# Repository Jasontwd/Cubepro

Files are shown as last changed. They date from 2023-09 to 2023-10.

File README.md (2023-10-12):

# Supercharged 3D Systems Cube Pro Trio
## New Twin hotend rebuild into a high temperature production printer

Having access to the high quality 3DXTech filaments meant that I could take an old Cube Pro Trio and turn it into a fast high-temperature production printer.  This means I can now use various types of filaments including water soluble supports. Including High Temp filaments up to 420deg C

This has taken my 3D printing to another level, and means there is less waste and less issues.  When it comes to filaments, you get what you pay for - so when quality matters, the 3DXTech filaments are fantastic. 

------------------------------------------------------------------------------------------------------------------------------------------------------------------------------------------------------------------------

## <b>History on this build</b>

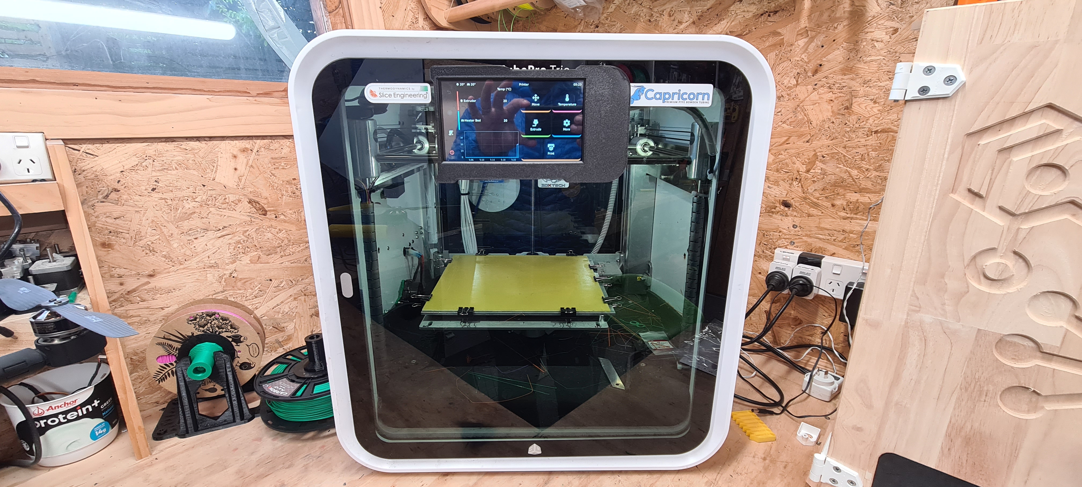
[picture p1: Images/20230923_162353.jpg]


These days there are lots of old 2nd hand printers out there in the market that sometimes need a new lease on life.

3D Systems produced their desktop Cube Pro Duo and trio several years ago and sent them off into mass manufacture.

They are out there for a good deal, if you are patient and can find one.  I found mine on Trade Me.  Also check out eBay and hit up your network.

Built like the proverbial 'brick shit house', these machines were slow but did a great job. The internal drive train, stepper motors, rails and enclosure are generally built very well, they form a solid basis of a good rebuild.

The professional looking enclosure is also well made, from Aluminum composite panel (ACP) with a LCD in built and glass door to top it all off.

Proprietary software and filament cases (with electronic chip) meant you where locked into their software and their filament.  In New Zealand it was hard to source filaments, which is frustrating and limits what you can do with the machine.

I found my printer on Trade Me in mid 2019, after a mate had also bought 2.

-----------------------------------------------------------------------------------------------------------------------------------------------------------------------------------------------------------------------------------
## <b>Specifications of the new machine, after its rebuild</b>

Cube Pro Duo Mosquito Liquid, water cooled high volume printer

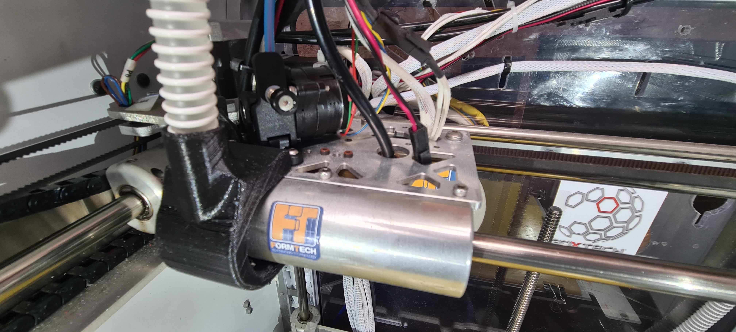
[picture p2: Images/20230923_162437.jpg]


Retrofitted electrics, Open Source main board with Raspberry Pi4 to complement the existing drive train on board the Cube Pro

- Klipper firmware and front panel klipper screen.
- Flyboard 64 main board.
- Raspberry PI 4 klipper headless on board, with wifi.
- Twin Liquid Mosquitos water cooled from Slice Engineering.
- 450deg rated heat blocks and heaters for PEKK etc.
- Obitor V2 twin extruders
- Heated 310mm square aluminum build plate 750w  230v AC bed ( 30sec heat up time to 120deg C)
- On board Rpi Camera wide angle for AI print detection
- High speed CPAP 12v part cooling fan
- 2 filament bays internal for pre drying capacity, great for ABS and Nylon 910 
- Enclosure ventilation suction fan 40mm rear mounted to external vent for ABS and PEKK printing
- Flexible filaments and water soluble supports printed easy as
- 24v 650w Power supply on board for all equipment, the existing one thats on the right.
- 5v PSU power supply on board for Rpi 4 (dedicated supply)
- Cube pro enclosure, insulated and isolated from electrics for heating enclosure internal for better fusion on prints.
- PEKK, PEEK and Carbon reinforced print ready
-------------------------------------------------------------------------------------------------------------------
## Water cooling
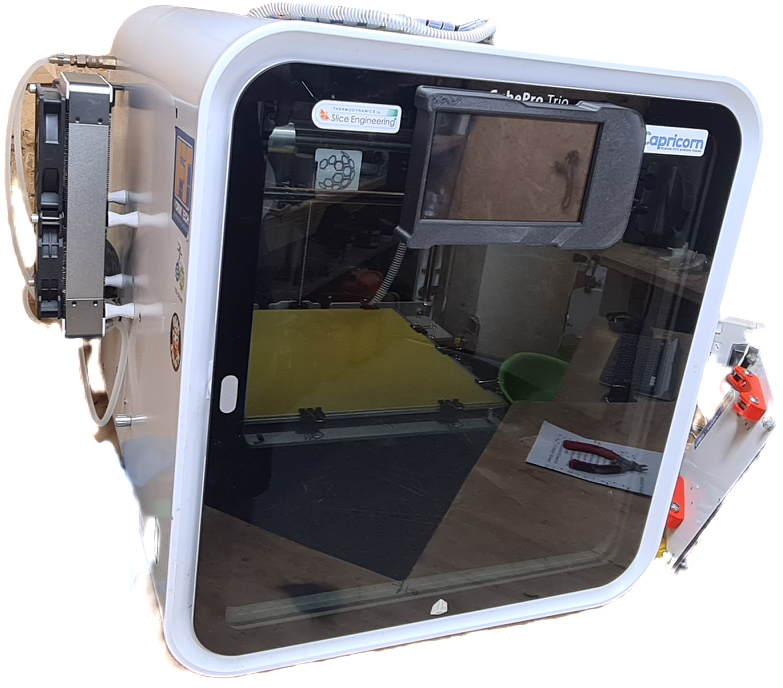
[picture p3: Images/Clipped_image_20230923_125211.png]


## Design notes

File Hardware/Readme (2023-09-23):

## CPAP Fans

Image of fan here:
https://www.aliexpress.com/item/33041228096.html?spm=a2g0o.order_list.order_list_main.21.68c11802tUSnGA

12mm CPAP hose locla to NZ
https://www.cpap.co.nz/collections/tubing/products/200-series-non-heated-tubing

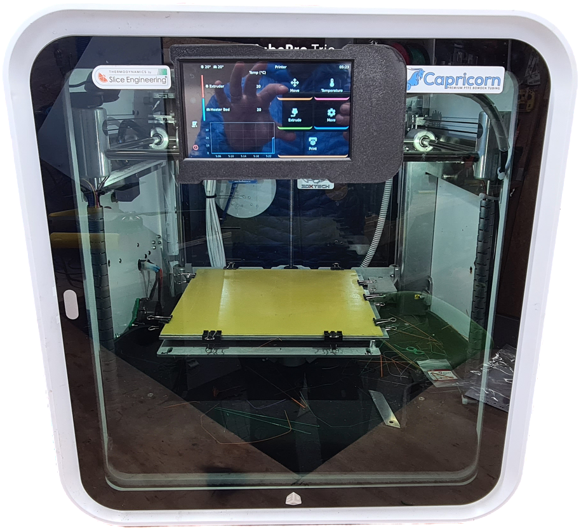
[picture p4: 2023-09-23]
Images/Clipped_image_20230923_163300.png

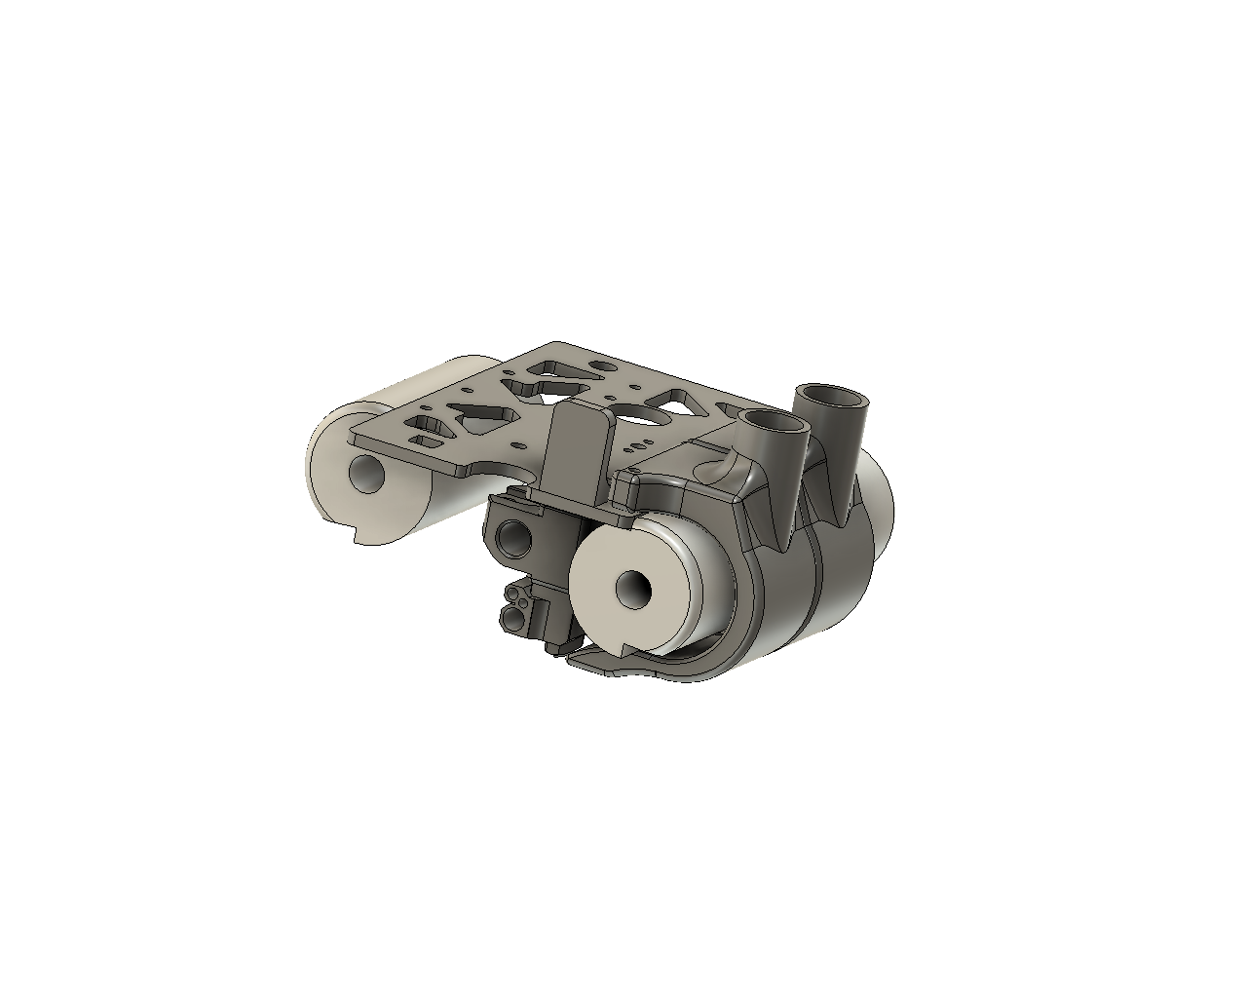
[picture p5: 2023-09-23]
CAD files/Isometric X gantry.png

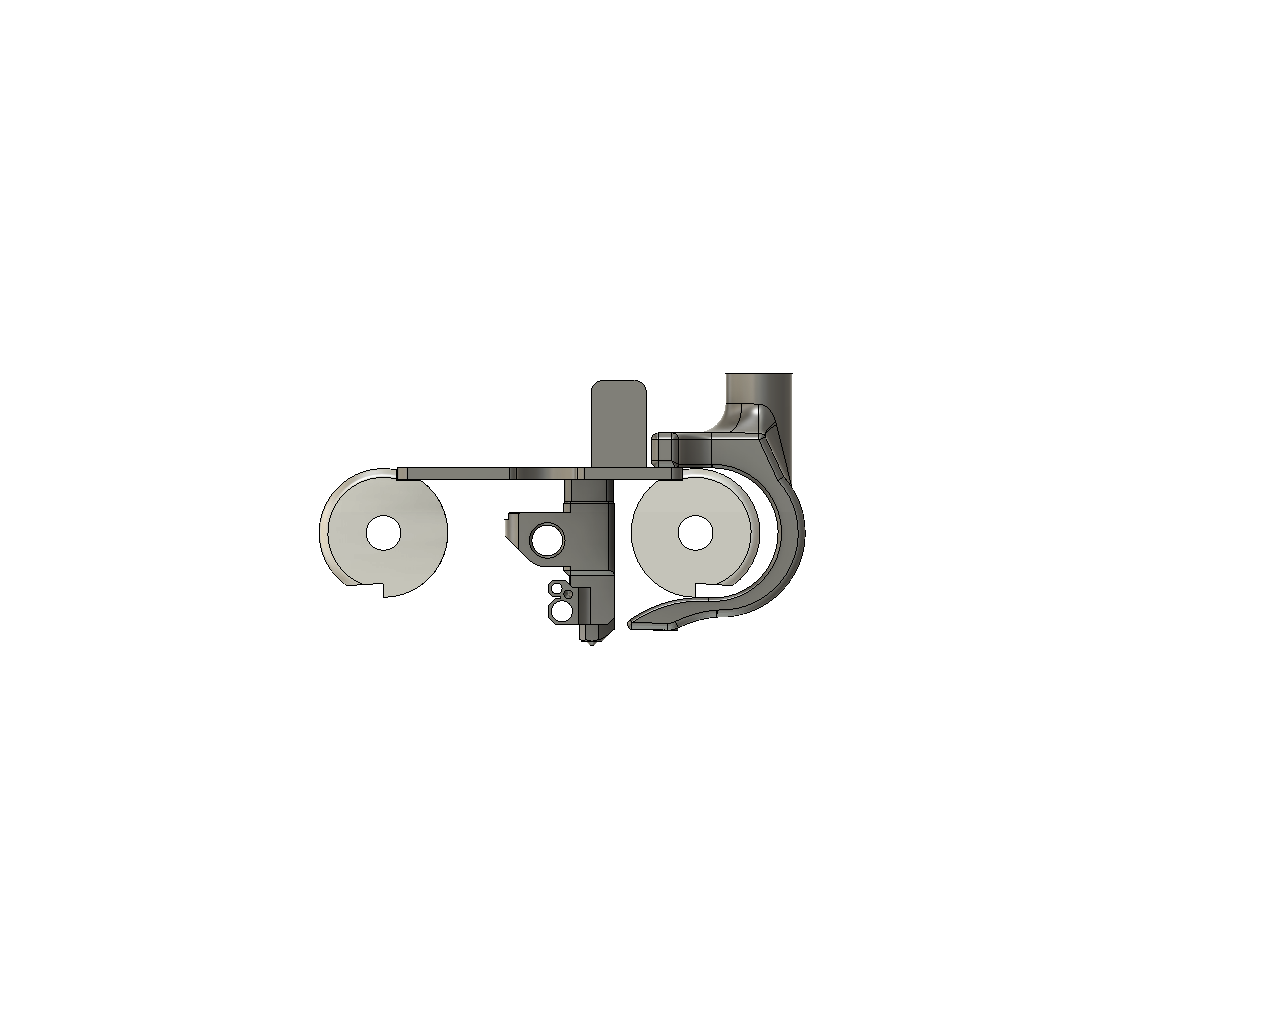
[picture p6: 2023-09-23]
CAD files/Side shot X gantry.png

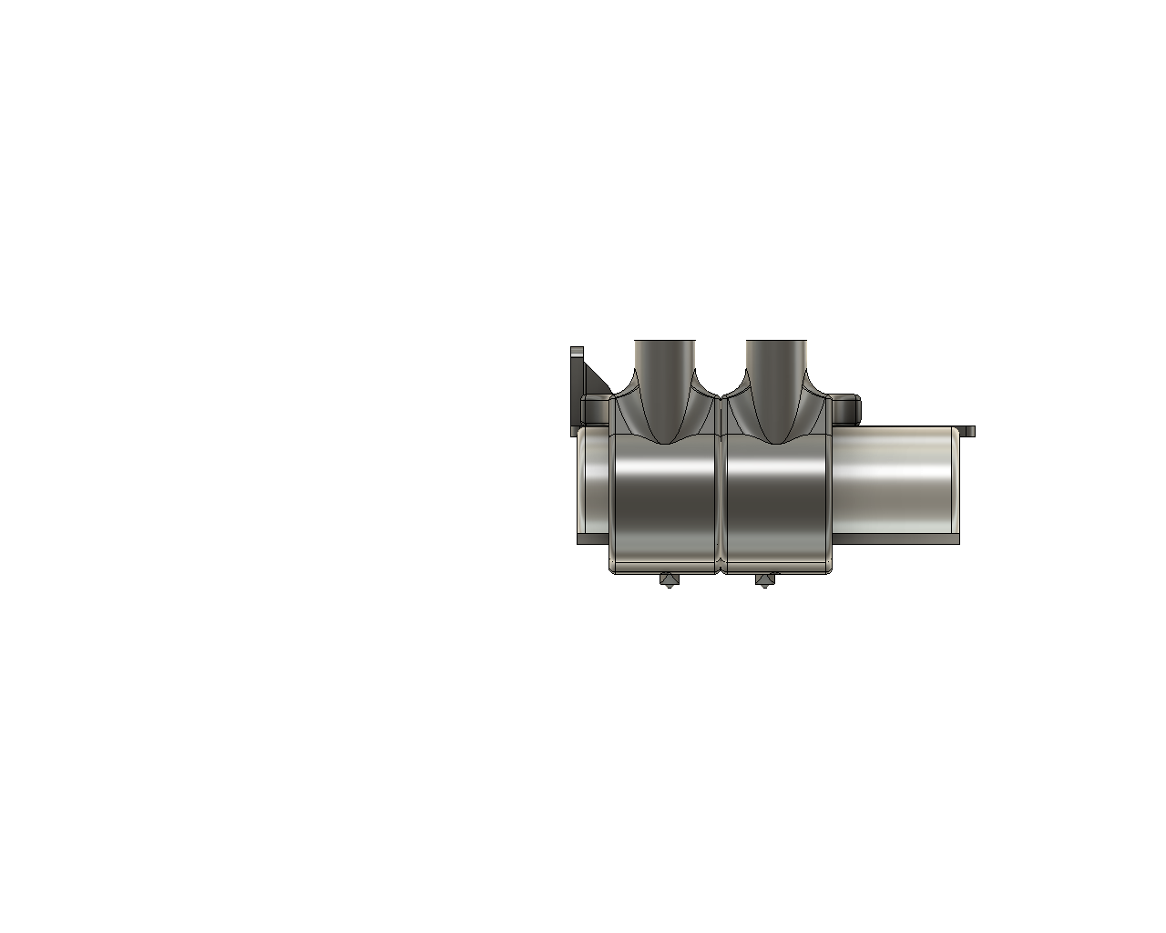
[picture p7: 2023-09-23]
CAD files/Front shot X gantry.png

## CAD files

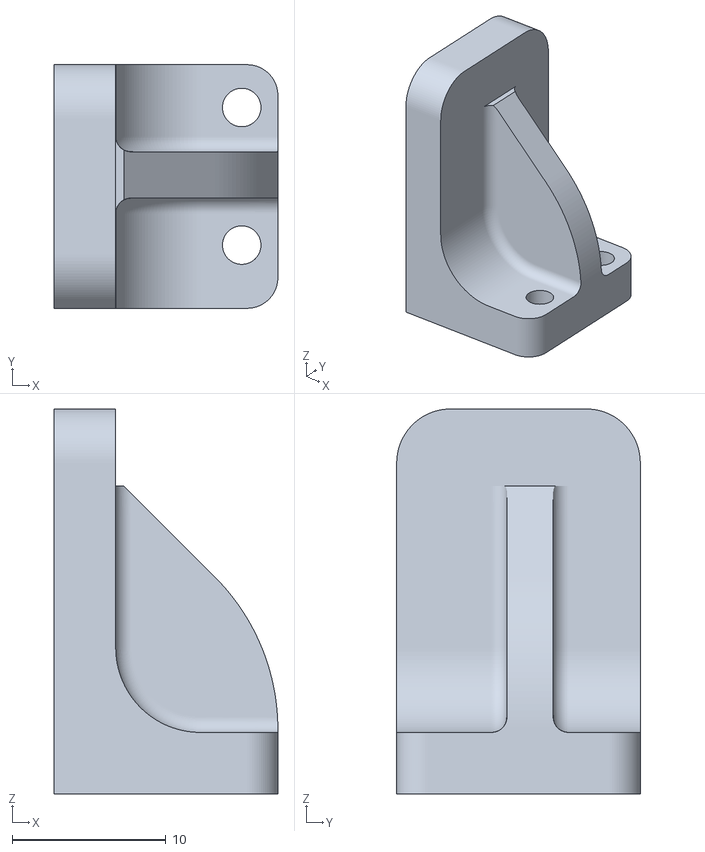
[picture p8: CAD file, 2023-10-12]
3D Printing files/X carridge endstop.stl
14.5 x 15.8 x 25.0

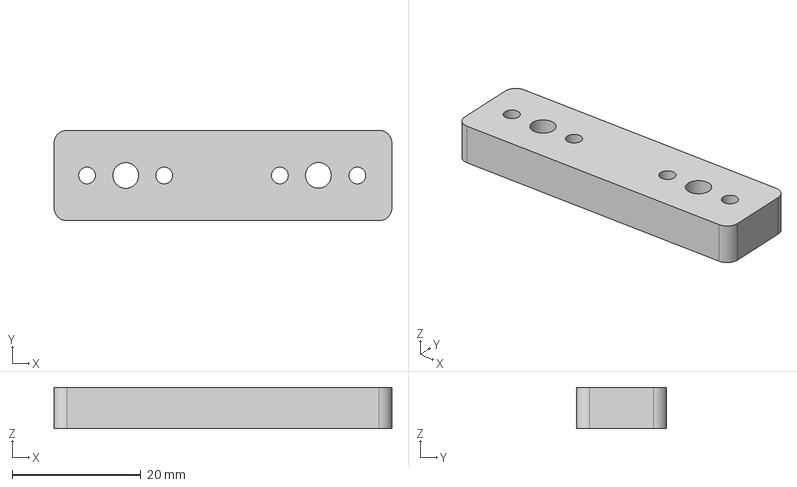
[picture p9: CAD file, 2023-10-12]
CAD files/mosquito shim 6.5mm.step
52.4 x 14.0 x 6.40 mm

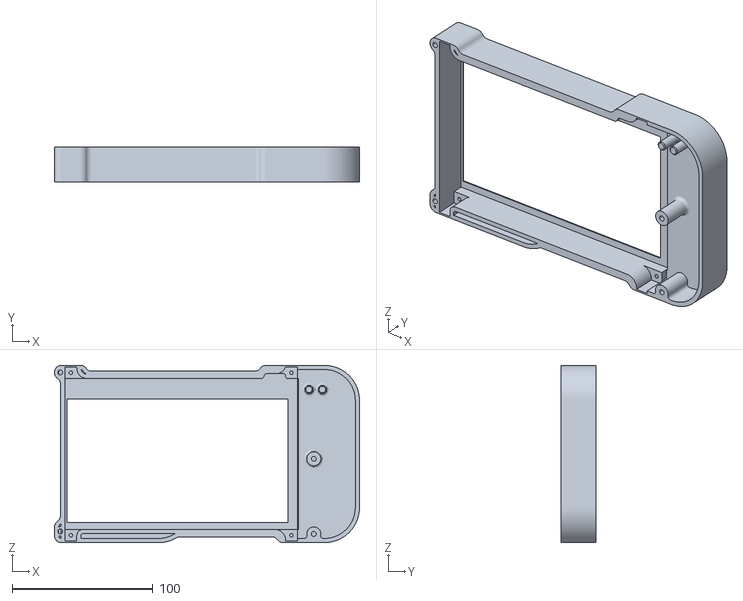
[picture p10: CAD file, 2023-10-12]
3D Printing files/Klipperscreen LCD front panel.stl
216.7 x 24.7 x 126.0

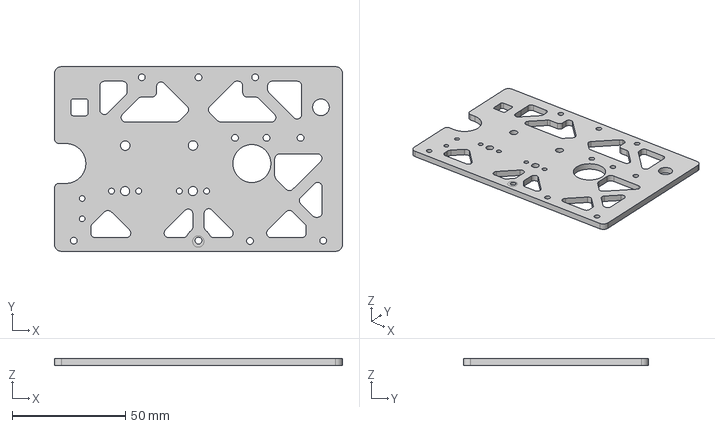
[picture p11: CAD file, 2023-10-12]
CAD files/X carridge mount cube pro aluminium CNC cut.step
127.0 x 81.4 x 3.25 mm

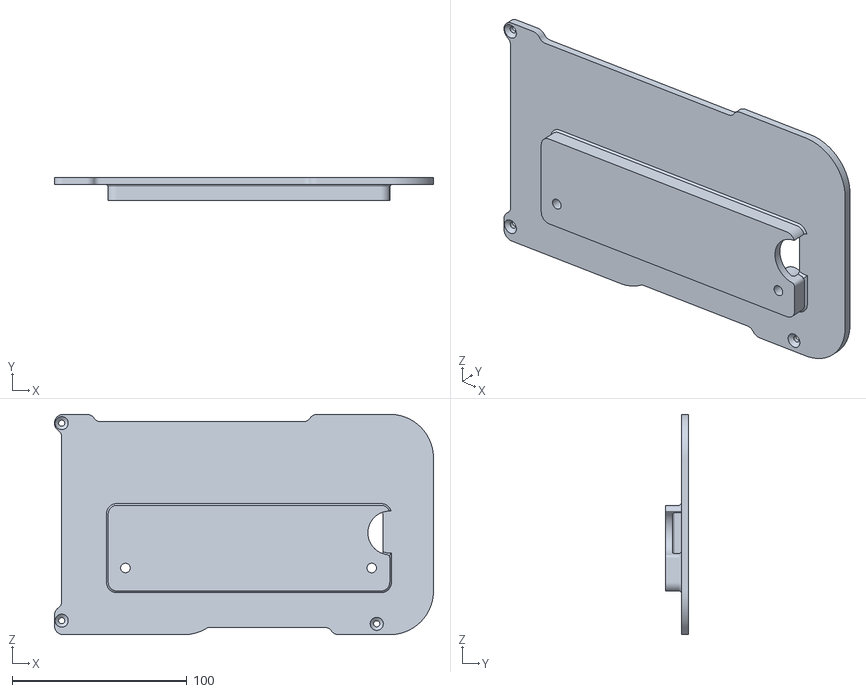
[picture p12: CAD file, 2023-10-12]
3D Printing files/Klipperscreen Back plate cubepro.stl
216.7 x 13.0 x 126.0

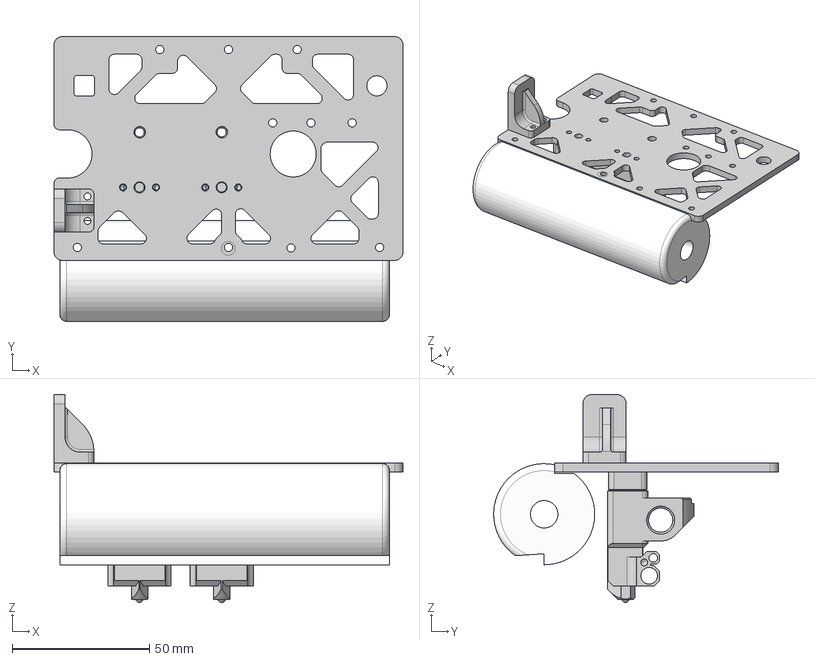
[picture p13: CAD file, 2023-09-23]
CAD files/CubePro replacement gantry plate to mount twin mosquito water cooled hotends.step
127.0 x 103.6 x 75.7 mm
mosquito liquid 1.75 (1) x 2
dragchain mount lower
endstop
mosquito shim 6.5mm

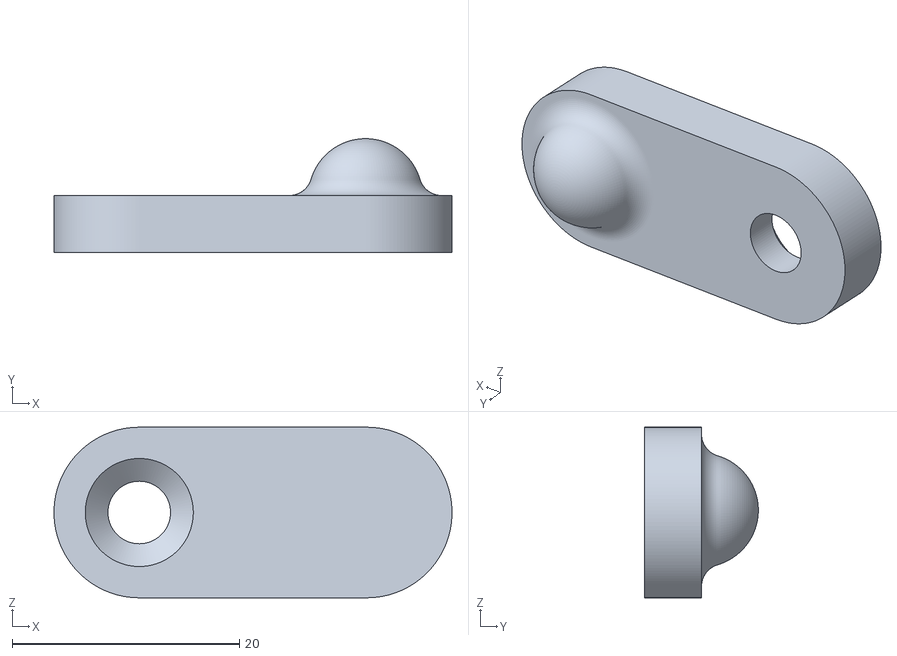
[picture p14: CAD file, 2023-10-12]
3D Printing files/Klipperscreen Backplate tabs ( print 2).stl
35.0 x 10.0 x 15.0

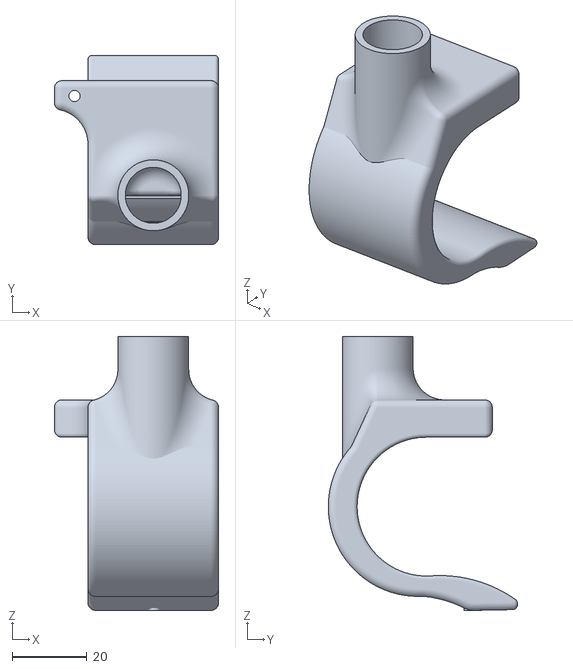
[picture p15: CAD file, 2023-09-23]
3D Printing files/CubePro fan duct left.stl
44.0 x 50.8 x 73.4

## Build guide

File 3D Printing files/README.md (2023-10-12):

Cubepro parts to print

Fan ducts print in heat proof plastic, suggest PA12 or SLS Nylons to help as its close to the bed and can warp with heat

KlipperScreen
Instructions: 
- All parts in CarbonX PLA or similar with PEI testured sheet for effect.
- Use the LCD screen from this address or Jaycar has the 7" touchscreens in stock
- https://www.jaycar.co.nz/1024x600-hdmi-7in-screen-with-usb-capacitive-touch/p/XC9026
- Buy a short HDMI cable and USB cable to run from the Rpi ( Klipper) to the screen in back plate
- Print out the left fan and mirror the right fan in the slicer

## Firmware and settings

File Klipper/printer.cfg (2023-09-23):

# Edited Jason Tweedie Formtech New Zealand 2023
[include mainsail.cfg]
[virtual_sdcard]
path: /home/pi/printer_data/gcodes
on_error_gcode: CANCEL_PRINT

[mcu]
serial: /dev/serial/by-id/<your-mcu-id>


[gcode_macro _CLIENT_VARIABLE]
gcode:
variable_use_custom_pos   : True ; use custom park coordinates for x,y [True/False]
variable_custom_park_x    : 120   ; custom x position; value must be within your defined min and max of X
variable_custom_park_y    : 10   ; custom y position; value must be within your defined min and max of Y
variable_custom_park_dz   : 10.0   ; custom dz value; the value in mm to lift the nozzle when move to park positi>
variable_retract          : 0.2   ; the value to retract while PAUSE
variable_cancel_retract   : 0.2   ; the value to retract while CANCEL_PRINT
variable_speed_retract    : 35.0  ; retract speed in mm/s
variable_unretract        : 0.2   ; the value to unretract while RESUME
variable_speed_unretract  : 35.0  ; unretract speed in mm/s
variable_speed_hop        : 15.0  ; z move speed in mm/s
variable_speed_move       : 70.0 ; move speed in mm/s
variable_park_at_cancel   : False ; allow to move the toolhead to park while execute CANCEL_PRINT [True/False]
variable_park_at_cancel_x : None  ; different park position during CANCEL_PRINT [None/Position as Float]; park_at>
variable_park_at_cancel_y : None  ; different park position during CANCEL_PRINT [None/Position as Float]; park_at>
## !!! Caution [firmware_retraction] must be defined in the printer.cfg if you set use_fw_retract: True !!!
variable_use_fw_retract   : False ; use fw_retraction instead of the manual version [True/False]
variable_idle_timeout     : 0     ; time in sec until idle_timeout kicks in. Value 0 means that no value will be >


[gcode_arcs]
resolution: 0.1
#   An arc will be split into segments. Each segment's length will
#   equal the resolution in mm set above. Lower values will produce a
#   finer arc, but also more work for your machine. Arcs smaller than
#   the configured value will become straight lines. The default is
#   1mm.


[stepper_x]
step_pin: PB9
dir_pin: PE0
enable_pin: !PE1
microsteps: 16
rotation_distance: 36.281
full_steps_per_rotation: 200
endstop_pin: !PC3
position_endstop: 0
position_max: 270
homing_speed: 50
homing_retract_speed: 5
#run_current: 0.9
#hold_current: 0.8
#interpolate: False
#stealthchop_threshold: 0

[stepper_y]
step_pin: PB8
dir_pin: PG11
enable_pin: !PG12
microsteps: 16
rotation_distance: 36.281
full_steps_per_rotation: 200
endstop_pin: !PF2
position_endstop: 265
position_max: 265
homing_speed: 50
homing_retract_speed: 5
#run_current: 0.9
#hold_current: 0.8
#interpolate: False
#stealthchop_threshold: 0

[stepper_z]
step_pin: PA8
dir_pin: !PD6
enable_pin: !PD7
microsteps: 32
rotation_distance: 3
full_steps_per_rotation: 200
endstop_pin: !PF0
position_endstop: 0
position_max: 220
homing_speed: 50
homing_retract_speed: 5
#run_current: 1.#run_current: 1.0
#hold_current: 0.8
#interpolate: False
#stealthchop_threshold: 0

[extruder]
step_pin: PC7
dir_pin: PD3
enable_pin: !PD4
microsteps: 16
rotation_distance: 4.637
full_steps_per_rotation: 200
#gear_ratio: 7.5:1
nozzle_diameter: 0.400
filament_diameter: 1.750
heater_pin: PF7 # Heat0
sensor_pin: PA0 # T1 Header
sensor_type: SliceEngineering 450
pressure_advance: 0.025 #to be calibrated
pressure_advance_smooth_time: 0.03
max_extrude_only_distance: 500
max_extrude_only_velocity: 120
#control: pid
#pid_Kp: 22.2
#pid_Ki: 1.08
#pid_Kd: 114
min_temp: 1
max_temp: 450

#[extruder1]
#step_pin: PC6
#dir_pin: PA15
#enable_pin: !PD0
#heater_pin: PF6 # Heat1
#sensor_pin: PC1 # T2
#...

#[extruder2]
#step_pin: PD15
#dir_pin: PG7
#enable_pin: !PG8
#heater_pin: PE6 # Heat2
#sensor_pin: PC0 # T3
#...

#[extruder3]
#step_pin: PD14
#dir_pin: PG4
#enable_pin: !PG5
#heater_pin: PE5 # Heat3
#sensor_pin: PF10 # T4
#...

#[extruder4]
#step_pin: PD13
#dir_pin: PD11
#enable_pin: !PG2
#heater_pin: PE4 # Heat4
#sensor_pin: PF5 # T5
#...

#[extruder4]
#step_pin: PD12
#dir_pin: PD8
#enable_pin: !PD9
#heater_pin: PE3 # Heat5
#sensor_pin: PF4 # T6
#...

[heater_bed]
heater_pin: PE2
sensor_pin: PF3 # T0
sensor_type: ATC Semitec 104GT-2
#control: watermark
min_temp: 0
max_temp: 160

[fan]
pin: PF8

[heater_fan fan1]
pin: PF9

#[heater_fan fan2]
#pin: PA2

#[heater_fan fan3]
#pin: PA1

#[heater_fan fan4]
#pin: PE13

#[heater_fan fan5]
#pin: PB11

[mcu]
serial:  /dev/ttyACM0

[printer]
kinematics: cartesian
max_velocity: 500
max_accel: 2000
max_accel_to_decel: 500
max_z_velocity: 15
max_z_accel: 15
SQUARE_CORNER_VELOCITY: 2

########################################
# TMC2208 configuration
########################################

[tmc2208 stepper_x]
uart_pin: PG13
run_current: 0.800
stealthchop_threshold: 0
interpolate: False

[tmc2208 stepper_y]
uart_pin: PG10
run_current: 1.2
stealthchop_threshold: 0
interpolate: False

[tmc2208 stepper_z]
uart_pin: PD5
run_current: 0.650
stealthchop_threshold: 0
interpolate: False

[tmc2208 extruder]
uart_pin: PD1
run_current: 0.800
stealthchop_threshold: 0
interpolate: False

#[tmc2208 extruder1]
#uart_pin: PA14
#run_current: 0.800
#stealthchop_threshold: 999999

#[tmc2208 extruder2]
#uart_pin: PG6
#run_current: 0.800
#stealthchop_threshold: 999999

#[tmc2208 extruder3]
#uart_pin: PG3
#run_current: 0.800
#stealthchop_threshold: 999999

#[tmc2208 extruder4]
#uart_pin: PD10
#run_current: 0.800
#stealthchop_threshold: 999999

#[tmc2208 extruder5]
#uart_pin: PB12
#run_current: 0.800
#stealthchop_threshold: 999999


########################################
# TMC2130 configuration
########################################

#[tmc2130 stepper_x]
#cs_pin: PG13
##diag1_pin: PC3
#run_current: 0.800
#stealthchop_threshold: 999999

#[tmc2130 stepper_y]
#cs_pin: PG10
##diag1_pin: PF2
#run_current: 0.800
#stealthchop_threshold: 999999

#[tmc2130 stepper_z]
#cs_pin: PBD5
##diag1_pin: PF0
#run_current: 0.650
#stealthchop_threshold: 999999

#[tmc2130 extruder]
#cs_pin: PD1
##diag1_pin: PE15
#run_current: 0.800
#stealthchop_threshold: 999999

#[tmc2130 extruder1]
#cs_pin: PA14
##diag1_pin: PE10
#run_current: 0.800
#stealthchop_threshold: 999999

#[tmc2130 extruder2]
#cs_pin: PG6
##diag1_pin: PC15
#run_current: 0.800
#stealthchop_threshold: 999999

#[tmc2130 extruder3]
#cs_pin: PG3
##diag1_pin: PC15
#run_current: 0.800
#stealthchop_threshold: 999999

#[tmc2130 extruder4]
#cs_pin: PD10
##diag1_pin: PC15
#run_current: 0.800
#stealthchop_threshold: 999999

#[tmc2130 extruder5]
#cs_pin: PB12
##diag1_pin: PC15
#run_current: 0.800
#stealthchop_threshold: 999999


########################################
# EXP1 / EXP2 (display) pins
########################################

[board_pins]
aliases:
    # EXP1 header
    EXP1_1=PB10, EXP1_3=PE14, EXP1_5=PE10, EXP1_7=PE8, EXP1_9=<GND>,
    EXP1_2=PE15, EXP1_4=PE12, EXP1_6=PE9,  EXP1_8=PE7, EXP1_10=<5V>,
    # EXP2 header
    EXP2_1=PB14, EXP2_3=PC5,  EXP2_5=PC4,  EXP2_7=PB2,   EXP2_9=<GND>,
    EXP2_2=PB13, EXP2_4=PF11, EXP2_6=PB15, EXP2_8=<RST>, EXP2_10=<GND>
    # Pins EXP2_1, EXP2_6, EXP2_2 are also MISO, MOSI, SCK of bus "spi2"

# See the sample-lcd.cfg file for definitions of common LCD displays.

# prime the nozzle
[gcode_macro PRIME_LINE]
gcode:
    M117 Prime Line
    G92 E0 ;Reset Extruder
    # move z axis
    G1 Z2.0 F2000 ;Move Z Axis down
    # move to prime position
    G1 X10 Y30 Z0.28 F2000.0 ;Move to start position
    G1 X10 Y200.0 Z0.28 F1500.0 E15 ;Draw the first line
    G1 X14 Y200.0 Z0.28 F2000.0 ;Move to side a little
    G1 X14 Y50 Z0.28 F1500.0 E30 ;Draw the second line
    G92 E0 ;Reset Extruder
    G1 Z2.0 F2000 ;Move Z Axis up

[gcode_macro BEDMAX_LOWER]
gcode:
     G90
     G1 Z220 F2000

[gcode_macro LOAD_FILAMENT]
gcode:
    # Set datum
    G90
    # Lower bed by 10mm
    G1 Z50 F2000
    # Move to spot to extrude into purge pot
    G1 X150 Y0 F2000
    # extrude nozzle at park spot for purge
    G1 E50 F300
    # Retract
    #G1 E-0.5 F1000

[gcode_macro UNLOAD_FILAMENT]
gcode:
    # Set datum 0,0
    G90
    # Lower bed by 10mm
    G1 Z50 F2000
    # Move nozzle to park spot for replacement
    G1  X150 Y0 F2000
    # retract filamant
    G1 E-60 F2000

#*# <---------------------- SAVE_CONFIG ---------------------->
#*# DO NOT EDIT THIS BLOCK OR BELOW. The contents are auto-generated.
#*#
#*# [heater_bed]
#*# control = pid
#*# pid_kp = 55.072
#*# pid_ki = 1.902
#*# pid_kd = 398.583
#*#
#*# [extruder]
#*# control = pid
#*# pid_kp = 25.193
#*# pid_ki = 1.084
#*# pid_kd = 146.436
#*#

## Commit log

2019-12-30 Create Silicone Heated Bed
2023-09-22 Add files via upload
    6061 Aluminium X axis gantry plate to suit:
    1. Twin or single mosquito hotends air cooled
    2. Twin water cooled mosquitos with 3/8 brass BSP spacer nipple
    3. Twin or single mosquito conductor hotends
    [gantry plate 6061 min.stl]
2023-09-22 Update and rename README.md to marlinsettings
2023-09-22 Create Gantry Parts
2023-09-23 Update Gantry Parts
2023-09-23 Create stl
2023-09-23 Create Marlin settings
2023-09-23 Rename marlin_configs to Marlin files/marlin_configs
2023-09-23 Rename Gantry Parts to Hardware/Gantry Parts
2023-10-12 Create Klipperscreen
